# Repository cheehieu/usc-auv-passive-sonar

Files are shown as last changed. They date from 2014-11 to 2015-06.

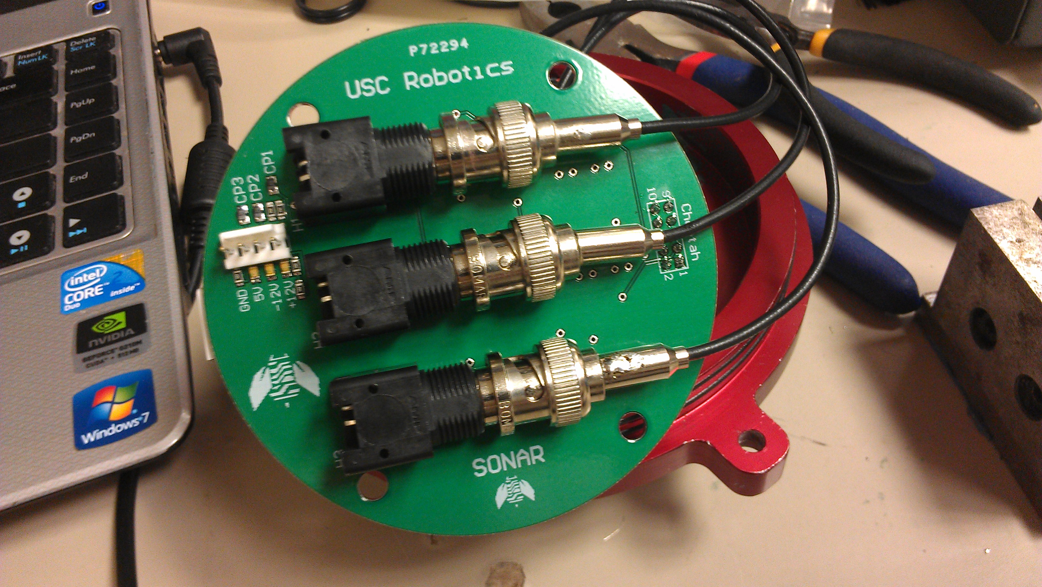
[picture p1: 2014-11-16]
images/IMAG0548.jpg

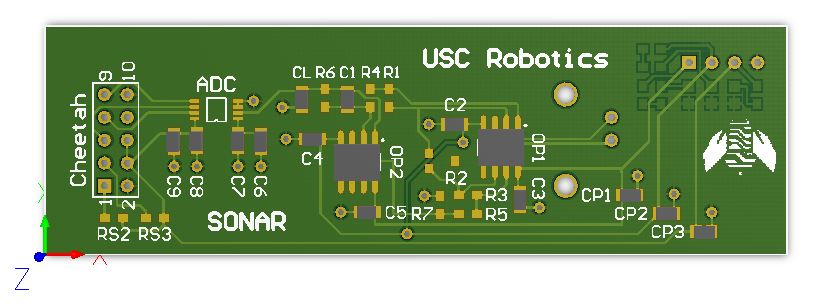
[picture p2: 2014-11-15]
images/sonarDAQ_single.JPG

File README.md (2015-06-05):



## Overview
One of the main tasks of the international AUVSI Robosub competition involves locating the source of an acoustic underwater pinger. This pinger is mounted somewhere on the floor of a 100m wide pool. It emits a 20-30kHz ping every 2 seconds for a duration of 1.3ms. The high level task is to use this ping signal to guide the AUV to a specific location in the pool. 

Our approach was to use an array of three hydrophones oriented in a precise geometric configuration, then use angle-of-arrival calculations to determine the direction of the ping source. To do this, we needed to ensure a clean analog signal from the hydrophones. A custom PCB was designed to perform high speed signal conditioning and data acquisition. This data could then be processed with a series of filters and phase comparisons, which result in ping detection and calculating a desired heading for the AUV.

Because this project spanned the mixed signal domain, a lot of prototyping and testing was done to ensure functionality. Below is an early stage whiteboarding of the signal path, from hydrophone input to robot actuation.



## Hardware
Like most electronic components on the AUV, the hydrophones and sonar board are housed in a double o-ring sealed cylindrical aluminium enclosure. Waterproof Fischer connectors are used to interface the power and data signals of the sonar board with the main CPU. The enclosure and hydrophones are mounted in an equilateral triangle configuration at the bottom of the AUV.

A previous approach to the passive sonar project involved using a triangular array of 3 hydrophones and passive electrical components to isolate and amplify the energy of a wave packet. The signals from the hydrophones were digitized using ADCs, and a Cheetah SPI Host Adapter (an off-the-shelf high-speed communication tool for facilitating the data streaming over an SPI serial bus). The digital information was processed by a microcontroller for its frequency content, and a ping-detection algorithm was used. This involved extracting the phase information and converting the time-difference-of-arrival into an angle towards the pinger. The main issues were signal strength and signal noise, as there appeared to be a lot of interference and cross-talk.



This time around, we are exploring two different approaches. One approach uses a narrow switched capacitor bandpass filter to isolate the 20-30kHz ping signal, an high-gain amplifier to clip the signal (essentially turning it into a square wave), and a phase comparator to determine the phase differences between the different hydrophone channels. The phase comparators will output a pulse width proportional to the phase difference, which is then read by an Arduino microcontroller.

The second approach is an analog frontend improvement of last year’s Cheetah solution. The grounds of each hydrophone channel will be kept separated, and differential-pair hardware will be used to reduce the interference, cross-talk, and external noise. The signals from the hydrophones can be very weak so a low-noise preamplifier will be used to boost and condition the signal for the bandpass filter. Also, faster and more precise ADCs will be used, and a fourth hydrophone will be incorporated into a tetrahedron-like configuration to add another dimension to our calculations.

A circular PCB was designed to fit into the small cylindrical enclosure and interface with all three hydrophones. One prototype is shown below from layout to board bringup.






## Software
Because the AUV ran on a ROS framework, the sonar node was written to post ROS messages to indicate signal strength and direction. The sonar software took many sample conversions from the ADCs through the high-speed SPI buffer on the Cheetah. The data points were analyzed for their frequency content using a digital fast Fourier transform and bandpass filters.

Here, some test data was saved into a CSV text file and plotted in Octave. The "Overlay" plot represents a phase comparison of the input subplot signals.



A windowing time binning algorithm was used to determine if the signal was indeed a ping. Using all data input streams from the three hydrophones, the signal phase can be compared to determine an angle-of-arrival.



## 3D
<iframe width="640" height="480" src="https://sketchfab.com/models/2c645406e3c548b1852d1a6a05af44f1/embed" frameborder="0" allowfullscreen mozallowfullscreen="true" webkitallowfullscreen="true" onmousewheel=""></iframe>

<p style="font-size: 13px; font-weight: normal; margin: 5px; color: #4A4A4A;">
    <a href="https://sketchfab.com/models/2c645406e3c548b1852d1a6a05af44f1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" target="_blank" style="font-weight: bold; color: #1CAAD9;">Passive Sonar PCB</a>
    by <a href="https://sketchfab.com/hieu?utm_source=oembed&utm_medium=embed&utm_campaign=2c645406e3c548b1852d1a6a05af44f1" target="_blank" style="font-weight: bold; color: #1CAAD9;">hieu</a>
    on <a href="https://sketchfab.com?utm_source=oembed&utm_medium=embed&utm_campaign=2c645406e3c548b1852d1a6a05af44f1" target="_blank" style="font-weight: bold; color: #1CAAD9;">Sketchfab</a>
</p>

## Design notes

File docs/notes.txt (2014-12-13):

3ADC ()
- input filtering with NPO and silvermica type dielectric capacitors, metal film resistors (pg. 12)
- input range from VGA (1.25V)
- 10uF ceramic or tantalum in parallel with .1uF ceramic capacitor for Vref->GND

- board layout
- PCB with ground plane
- separate analog and digital signal lines
- 10uF surface mount AVX capacitor for VDD (Murata GRM219R60J106M)
- 0.1uF ceramic capacitor for VREF
- capacitors located as close to pins as possible (keep traces short and wide as possible)

VGA (AD8331)
- Each channel contains an LNA that provides user-adjustable input impedance termination, a differential X-AMP VGA, and a pro-grammable gain postamp with adjustable output voltage limiting
- hydrophones have a 1kohm impedance at desired frequencies
- HILO, GAIN, VCM (adjust to 1.5V for 3V ADC)
- values of RFM and CSH, based on LNA input impedance
- VCM, RCLMP, driving 3V ADC's
- get rid of some jumpers to save space

- board layout
- multilayer board with power and ground planes recommended
- blank areas in the signal layers filled with ground plane
- decoupling SM caps for power supply pins
- decoupling ferrite beads for LNA power pins
- 5V regulator for VGA array
- LON/LOP traces as short as possible for coupling caps
- Riz placed near LON pin
- resistors placed close to VGA output pins, VOL/VOH
- short signal traces

Voltage Reg
- aluminum electrolytic or tantalum capacitors
- effective series resistance greater than 0.1ohm, less than 5ohm

Lowpass filter to remove high frequency noise?
BNC connector footprint (vertical or right angle?)
//Hard-wire jumpers
Figure out VGA and ADC special inputs/outputs
Mounting drill holes
Arduino pin to LED
Trace length for diff pairs (VGA to ADC)
Place ADC on back of board (upside down)
Arduino's max PWM frequency is 62500Hz
Cheetah and Arduino header connectors spacing
Include low pass (band pass filter)
Thicker power and ground traces
Fix Gain2 LPF

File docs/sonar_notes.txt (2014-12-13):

10Mhz Cheetah clock
3kHz sine wave, 1VPP
+/- 2.5V input
clipping?

Reading data from an ADC with the Cheetah:
---SET UP COMMAND QUEUE---
- Call ch_spi_queue_clear to clear the command queue.
- Call ch_spi_queue_oe to add a command to the queue to enable the Cheetah device’s outputs on the SPI bus.
- Call ch_spi_queue_ss to add a command to the queue to enable the slave select signal.
- Call ch_spi_queue_byte and ch_spi_queue_array to queue data to be sent across the SPI bus
- Call ch_spi_queue_ss to queue a command to disable the slave select signal
- Optionally, call ch_spi_queue_oe to queue a command to disable the outputs of the Cheetah device.
- Call ch_spi_batch_shift to send the accumulated accumulated commands across the SPI bus.

Note:
Please note that the queue is not cleared after it has been executed. This allows the same
queue to be executed multiple times without re-queuing commands. The only way to clear a
queue is by calling ch_spi_queue_clear.

If the user wishes to repeat the exact same shift sequence on the bus, the last step can be
executed without the preceding ones. Also, the OE enable commands and SS assert/deassert
commands are held persistent on the Cheetah device. 

---SEND SEVERAL SEPARATE SPI PACKETS---
1. Assert the OE.
2. Assert the appropriate SS, queue the data, and deassert SS.
3. Add optional delay on the bus.
4. Assert the appropriate SS, queue the data, and deassert SS.
5. Repeat the last two steps as many times as desired.
6. Call the batch shift function.

There is an alternative, non-blocking implementation that
can be used in lieu of ch_spi_batch_shift. The functions ch_spi_async_submit and
ch_spi_async_collect allow the user to submit a batch queue and perform other tasks (including
assembling and submitting a subsequent queue) before collecting the results of the initial SPI shift operation. 

---PROCESSING ASYNC DATA---
1. Submit 2–4 asynchronous batches, each with about 40 ms worth of SPI shifting. A single batch can contain many SPI commands / packets, of course.
2. Call ch_spi_async_collect to collect one batch. Signal another thread to process this data.
3. Submit another asynchronous batch to replace the one that was just collected.
4. Repeat steps 2 & 3 while your other thread simply processes the data.

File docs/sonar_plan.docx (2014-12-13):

SONAR PROJECT

Test Bed Design

- Oscillator board
- Phase difference board
  - phase shift board to simulate pinger location
  - function generator tests

Analog Board

- ~~Hydrophone maintenance~~
  - ~~(3x) RESON TC4013 Hydrophones~~
  - ~~Spaced 24mm apart in triangle at bottom of sub~~
- ~~Pinger~~
  - ~~Output:~~ ~~22, 23, 24, 25, 26, 27, 28, 29 or 30 kHz~~
  - ~~Pings at 0.5 Hz (2 seconds) for 1.3ms with a sound level of 187 dB~~
  - ~~Separated by 0.9 seconds from practice pool ping~~
- Filter Design
  - Switched Capacitor Filter
    - Narrow bandpass for 20Khz to 40Khz range
    - Controlled by clock frequency in the 0-40Mhz range
    - MAX263
      - Supply voltage: 15V
      - Clock input (2.4min High, 0.8max Low)
  - Infinite Gain Amplifier
    - opamp
  - Phase Difference

Digital Board

- Microcontroller Board (interface with phase diff)
- Programmable Oscillator
  - Maxim DS1077, DS1085
  - Frequency range of 66-133MHz, adjustable over the I2C connection in 10KHz intervals
  - This is fed into a programmable divisor of 1-1025, making for a wide range of available output values
  - Pinout, voltage/current requirements
- Carrier Board >> Arduino >> Progammable Oscillator >> Switched Capacitor Filter
- Microcontroller software (Arduino)

ROS Sonar Node

- Messages (Dave’s implementation)
  - Pinger ID (#0 correct, #1 incorrect)
  - Heading
  - Magnitude
  - TimeSince
- PingerArray

Pinger >> water >> hydrophones >> VGA >> filter >> ADC >> Cheetah SPI >> ROS Sonar Node

Pinger >> water >> hydrophones >> preamp >> filter >> opamp >> ADC >> Cheetah SPI >> Sonar Node

Pinger >> water >> hydrophones >> preamp >> filter >> >> opamp >> phase comparator >> ADC >> Sonar Node

~~Pinger operation (~~~~turn on,~~ ~~set frequency, mount underwater~~~~, two~~ ~~pingers~~~~, interference~~~~)~~

~~Signal capture through hydrophones/connecters~~ ~~(compare/test signal amplitudes, signal degradation?)~~

~~Pre-amp to boost signal for filter?~~ ~~VGA~~~~. Signal conditioning~~

Signal filtering (test for filtered output, add noise)

- Switched cap filter input (function generator sine wave at 25kHz, 100mV)
- Clock input (function generator, square wave at 1MHz, 5V, interface with oscillator after)
- Variable frequency oscillator
- Supply voltage, control words (pin programmable with Arduino), operating modes, Qs, fclk/f0 ratio, cascading?
- MAX7490

Amplification

- Input (func gen to simulate filtered signal)
- Op-amp (gain to clip signal and turn into square wave), differential amplifier for low noise
- Zero crossing detector, rectifier, multilateration

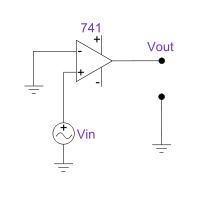
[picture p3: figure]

- San Diego City used 100X gain

Filtered signal acquisition (ADCs, Cheetah sampling)

- Hook up ADC to func gen (DC voltage, sinusoid, square wave)
- Arduino to take in bytes from ADC (plot and verify)
- Repeat with Cheetah at faster sampling rates
- AD7865 simultaneous sampling four channel 14-bit ADC
- Clipped input from amplifier does not exceed voltage requirements? Clamping? Op-amp supply voltage
- FFT to find phase difference

Phase comparator

- Outputs a PWM signal whose pulse width is proportional to the difference in phase between the two signals
- MAX9382
- PWM signal goes to microcontroller to determine how long the pulse width is
- Pulse width is converted to a left or right degree error (directional error) by a look up table
- San Diego city uses 4 hydrophones mounted at 45 degrees to vertical, to determine when sub is right above the pinger
- PLL phase locked loop
  - A type II detector is sensitive only to the relative timing of the edges of the input and reference pulses, and produces a constant output proportional to phase difference when both signals are at the same frequency.

Ping detection (measure length of time, bin, windows)

- Analog voltage threshold triggers sampling and storing in serial memory
- Cross-correlation algorithm is performed on binned signal return samples to find phase differences
- Wait for min amplitude, accumulate samples, apply band pass filter on samples, calculate phase difference between hydrophones (reference channel and remaining), send phase difference, compare in lookup table for heading and elevation (value in the table with smallest difference)

Phase difference analyzer (angle-of-arrival calculation, closest hydrophone pair, 3rd hydrophone)

- From each hydrophone pair, two candidate rotation angles are found. The two angles which are closest to each other gives the final estimate of rotation needed to aim toward the pinger

Localization (sensor data for direction, phase difference tells you distance from source)

Test on SeaBee

Run 3-channels, triangulation

Analog filtering, digital signal processing

Cornell can compute heading and elevation to the pinger within one degree (4 hydrophones)

Hyperbolic positioning to determine directional vector towards the pinger

Distance between hydrophones is less than half the wavelength, to ensure unambiguous phase difference → along with physical placement of h-phones and speed of sound underwater, can determine the time difference and calculate angle of sound source

FPGA? DSP?

repurpose VGA for pressure sensor?

Parts lists and cost breakdown

Break up into smaller tasks (amplifier, phase comparator, ADC, find pinger)

Jose
Current Milestone: Finish bandpass filter
Date: October 11th

Dylan
Current Milestone: Test bed oscillator
Date: September 20th

I'll start with the system as it was for the competition last year:

Hardware:

- (3x) RESON TC4013 Hydrophones (http://www.reson.com/wp-content/uploads/2010/12/TC4013.pdf)
- Cheetah SPI Host Adapter (http://www.totalphase.com/products/cheetah_spi/)
- LTC1400 12-Bit, 400ksps ADC (http://cds.linear.com/docs/Datasheet/1400fa.pdf)
- Custom PCB (Beosub Repository)
  - trunk/Electrical/Eagle/Wave Packet Sonar/SonarCheetah.brd
  - trunk/Electrical/Eagle/Wave Packet Sonar/SonarCheetah.sch

Signal Path:

Pinger >> ~~~ water ~~~ >> hydrophones >> ADC >> Cheetah SPI >> ROS Sonar Node

Software:

- Initial Dev
  - Saliency Repository
    - src/Robots/SeaBeeIII/Sonar
- Current
  - ROS Node (http://code.google.com/p/seabee3-ros-pkg/)
- FFTW3 - FFT Library (http://www.fftw.org/)

Walkthrough:

- The initial dev software folder contains all of the testing software and development/experimentation code I initially used to determine how to approach coding the phase difference algorithm, frequency testing, Cheetah communications, etc...
- The ROS node is the most current version of the code (originally written for Box Turtle, but should be ok with C Turtle as well)
- Cheetah SPI (as configured in ROS node code)
  - NOTE: At the time only the 32-bit pre-compiled shared library was provided, so be aware of this when running / compiling on 64-bit systems
  - Communicates in asynchronous mode to keep actual sampling rates up
  - "True" sampling rate is calculated based on the speed of the Cheetah at runtime using a linear interpolation method from experimental data (signal generator, spectrogram, and max frequency bin identifier)
    - Initially I tried calculating this real-time in the principle loop but had major inaccuracies
    - Talked with Rand & Edward about it, but didn't come up with a function fix / solution, so went with the existing approximation
  - Uses slave select (SS) signals as convert (CONV) signals for ADCs
  - Generates a batch of conversions, which will occur in rapid succession without interruption once submitted
  - The collected data stream comes back as individual bytes, but the ADC output data is a combination of two consecutive bytes and must be combined so relevant information can be extracted (data, ready bit, etc.) See ADC data sheet for spec and code for implementation
  - The extracted (valid) data is stored in their respective signal buffers corresponding to the 3 hydrophones
- Ping Detection
  - Each buffer is examined with a short sliding window for significant frequency content in the expected FFT bin
    - Since the window is short, the frequency resolution is poor but the temporal resolution is high so a full ping can be isolated in time with reasonable granularity
  - A running sample mean is kept to evaluate whether or not the current value of the FFT bin is large enough to be considered a peak
  - If peaks are found in all channels, an indicator is noted for that time step
    - This continues until the current time step does not have an indicator
  - Once a peak is not detected, the run of indicators is checked for sufficient length (i.e. was it a full ping, or just a small error)
  - The history data corresponding to all blocks marked with a positive indicator are extracted an an FFT is performed on the full ping sequence
    - The increased length of the FFT will provide more accurate frequency resolution and allow the phase information from just the ping frequency to be extracted
- Angle Calculation
  - An optimal-pair phase difference angle-of-arrival (http://en.wikipedia.org/wiki/Angle_of_arrival) algorithm was developed by Rand and I for relative angle estimation of sonar pingers
  - The best hydrophone pair is determined by finding the minimum phase difference between hydrophone pairs
  - The phase difference is adjusted for a phase factor (rear vs. front) using the remaining hydrophone
  - The phase difference is adjusted for an angular offset base on the chosen hydrophone pair
  - Angle estimate is calculated using the physical separation of the hydrophones

Problems:

- Signal strength
  - When the cables were redone just before the competition, the signal strength dropped significantly to the point that the peak detection stopped working
  - The cable attachements need to be redone and the analog front end (following section) will help with this
- Signal quality (SNR)
  - Without hardware filtering, the only signal isolation occurs through the FFT
  - Ambient noise and common hydrophone grounds cause significant phase distortions that decrease the accuracy of the angle estimate

Now the more recent work & future directions:

Proposed New Hardware (Experimental):

- LTC1569CS8-7 - Linear Phase, DC Accurate, Tunable 10th Order Lowpass Filter (http://cds.linear.com/docs/Datasheet/15697fs.pdf)
- AD8331ARQZ-ND - Single Variable-Gain Amplifier (VGA) with Ultralow Noise Preamplifier and Programmable RIN (http://www.analog.com/static/imported-files/Data_Sheets/AD8331_8332_8334.pdf)
- LTC1403ACMSE-1 - Serial 14-Bit, 2.8Msps ADC (http://www.linear.com/pc/downloadDocument.do?navId=H0,C1,C1155,C1001,C1158,P2481,D1475)
- Simple Arduino / Amtel chip to sample the signal path & control the VGA

This set of hardware was my initial suggestion for a revised analog frontend that filters out high-frequency noise (tunable filter), keeps the signal amplitude high (VGA), and samples with more precision at higher frequency (new ADC). I'm happy with the idea, but I think to really address the problems we had with the sampling we need to use differential pair hardware and separate the grounds of the signal channels, which should remove a significant amount of interference; Since the signal paths would be independent differential pairs, the cross-talk & external noise will essentially be removed. More research needs to be done to figure out what hardware should be used.

Signal Path:

Pinger >> ~~~ water ~~~ >> hydrophones >> VGA >> filter >> ADC >> Cheetah SPI >> ROS Sonar Node

DIAGNOSTIC BOARD

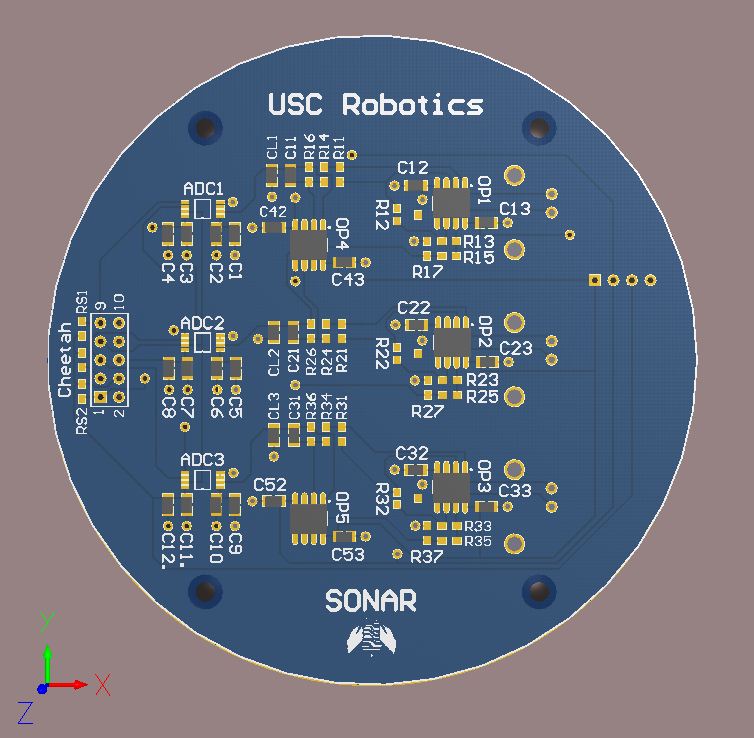
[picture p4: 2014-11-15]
images/sonarDAQ.JPG

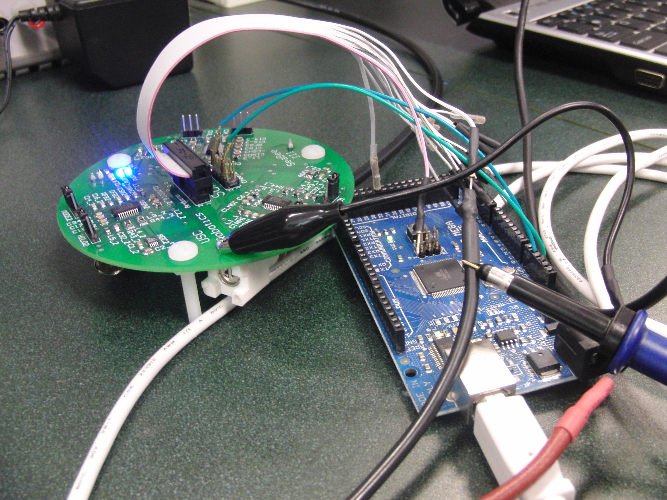
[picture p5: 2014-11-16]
images/CIMG1183.JPG

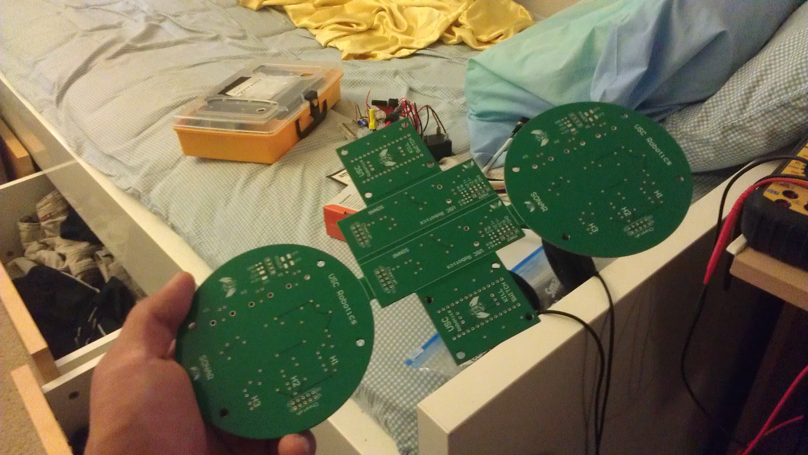
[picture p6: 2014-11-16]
images/IMAG0600.jpg

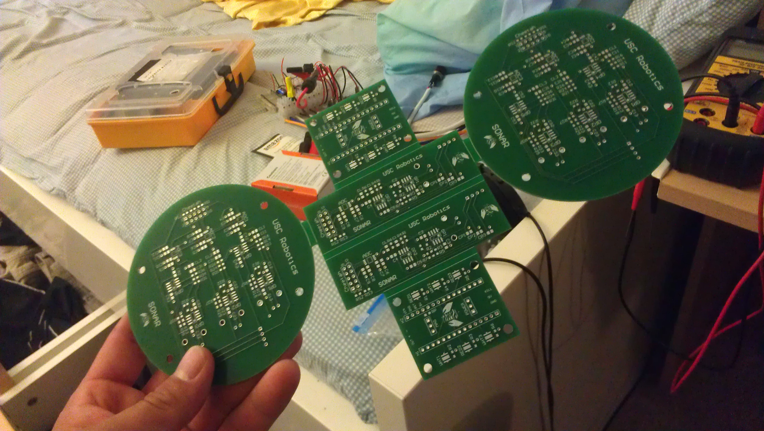
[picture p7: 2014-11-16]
images/IMAG0599.jpg

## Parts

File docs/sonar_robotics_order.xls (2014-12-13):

USC Aerial Robotics
Order Date: 2/1/2012
Part # | Item | Qty | Unit Cost | Total Cost | Link/Order Instruction | Purpose | Payment
Digikey.com
A32261-ND | BNC Female Connector | 5 | $3.48 | $17.40 | http://search.digikey.com/us/en/products/5227161-9/A32261-ND/811159 | Sonar | AMEX
493-4091-1-ND | 2.2uF Tantalum Cap | 10 | $0.46 | $4.60 | http://www.digikey.com/product-detail/en/F920J225MPA/493-4091-1-ND/2529818 | Sonar | AMEX
160-1416-1-ND | 0805 LED | 10 | $0.38 | $3.80 | http://www.digikey.com/product-detail/en/LTST-C170KSKT/160-1416-1-ND/386780 | Sonar | AMEX
490-4612-1-ND | Trimmer Pot | 10 | $0.44 | $4.40 | http://www.digikey.com/product-detail/en/PVZ3G104C01R00/490-4612-1-ND/1203955 | Sonar | AMEX
490-1673-1-ND | 0.1uF Ceramic Cap | 14 | $0.06 | $0.78 | http://search.digikey.com/us/en/products/GRM21BR71E104KA01L/490-1673-1-ND/587412 | Sonar | AMEX
493-2939-1-ND | 4.7uF Electrolytic Cap | 14 | $0.96 | $13.44 | http://www.digikey.com/product-detail/en/F951C475MPAAQ2/493-2939-1-ND/1129228 | Sonar | AMEX | case code P
490-1593-1-ND | 47pF Cap | 10 | $0.37 | $3.72 | http://www.digikey.com/product-detail/en/GRM2195C2A470JZ01D/490-1593-1-ND/587798 | Sonar | AMEX | grm219
490-1664-1-ND | 0.01uF Cap | 10 | $0.04 | $0.39 | http://www.digikey.com/product-detail/en/GRM216R71H103KA01D/490-1664-1-ND/587472 | Sonar | AMEX | grm216, pg8
P10KACT-ND | 10K Resistor | 20 | $0.10 | $2.00 | http://www.digikey.com/product-detail/en/ERJ-6GEYJ103V/P10KACT-ND/43118 | Sonar | AMEX
P1.0KACT-ND | 1K Resistor | 50 | $0.10 | $5.00 | http://www.digikey.com/product-detail/en/ERJ-6GEYJ102V/P1.0KACT-ND/42833 | Sonar | AMEX
LT1113CS8#PBF-ND | SM Opamp | 13 | $6.53 | $84.89 | http://search.digikey.com/us/en/products/LT1113CS8%23PBF/LT1113CS8%23PBF-ND/894415 | Sonar | AMEX
 |  | Order Total: |  | $140.42 | Plus Shipping

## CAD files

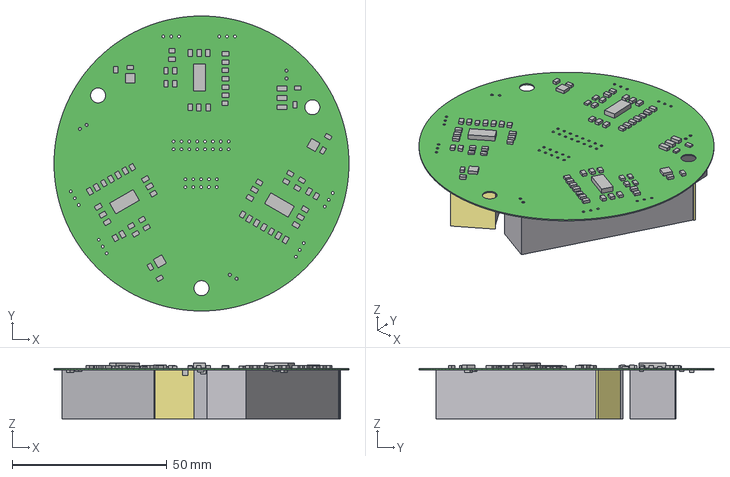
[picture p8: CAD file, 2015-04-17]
hw/Sonar/PCB/sonar.step
95.3 x 95.3 x 18.0 mm
Board
Extruded x 91

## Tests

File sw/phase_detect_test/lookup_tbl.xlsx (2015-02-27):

Phase Difference | PC1 (exp) | PC1 (act) | PC3 (exp) | PC3 (act)
0 | 0.000 | 0.000 | 0.000 | 0.000
10 | 0.278 |  | 0.139
20 | 0.556 | 0.591 | 0.278 | 0.264
30 | 0.833 | 0.767 | 0.417 | 0.367
40 | 1.111 | 0.929 | 0.556 | 0.425
50 | 1.389 | 1.065 | 0.694 | 0.523
60 | 1.667 | 1.266 | 0.833 | 0.616
70 | 1.944 | 1.393 | 0.972 | 0.709
80 | 2.222 | 1.564 | 1.111 | 0.792
90 | 2.500 | 1.730 | 1.250 | 0.865
100 | 2.778 | 1.906 | 1.389 | 0.943
110 | 3.056 | 2.087 | 1.528 | 1.036
120 | 3.333 | 2.219 | 1.667 | 1.119 | 1.603
130 | 3.611 | 2.385 | 1.806 | 1.183 | 1.784
140 | 3.889 | 2.581 | 1.944 | 1.261 | 1.945
150 | 4.167 | 3.994 | 2.083 | 1.354 | 2.063
160 | 4.444 | 3.930 | 2.222 | 1.437 | 2.214
170 | 4.722 | 3.915 | 2.361 | 1.515 | 2.361
180 | 5.000 |  | 2.500
190 |  |  | 2.639
200 |  |  | 2.778
210 |  |  | 2.917
220 |  |  | 3.056
230 |  |  | 3.194
240 |  |  | 3.333
250 |  |  | 3.472
260 |  |  | 3.611
270 |  |  | 3.750
280 |  |  | 3.889
290 |  |  | 4.028
300 |  |  | 4.167
310 |  |  | 4.306
320 |  |  | 4.444
330 |  |  | 4.583
340 |  |  | 4.722
350 |  |  | 4.861
360 |  |  | 5.000

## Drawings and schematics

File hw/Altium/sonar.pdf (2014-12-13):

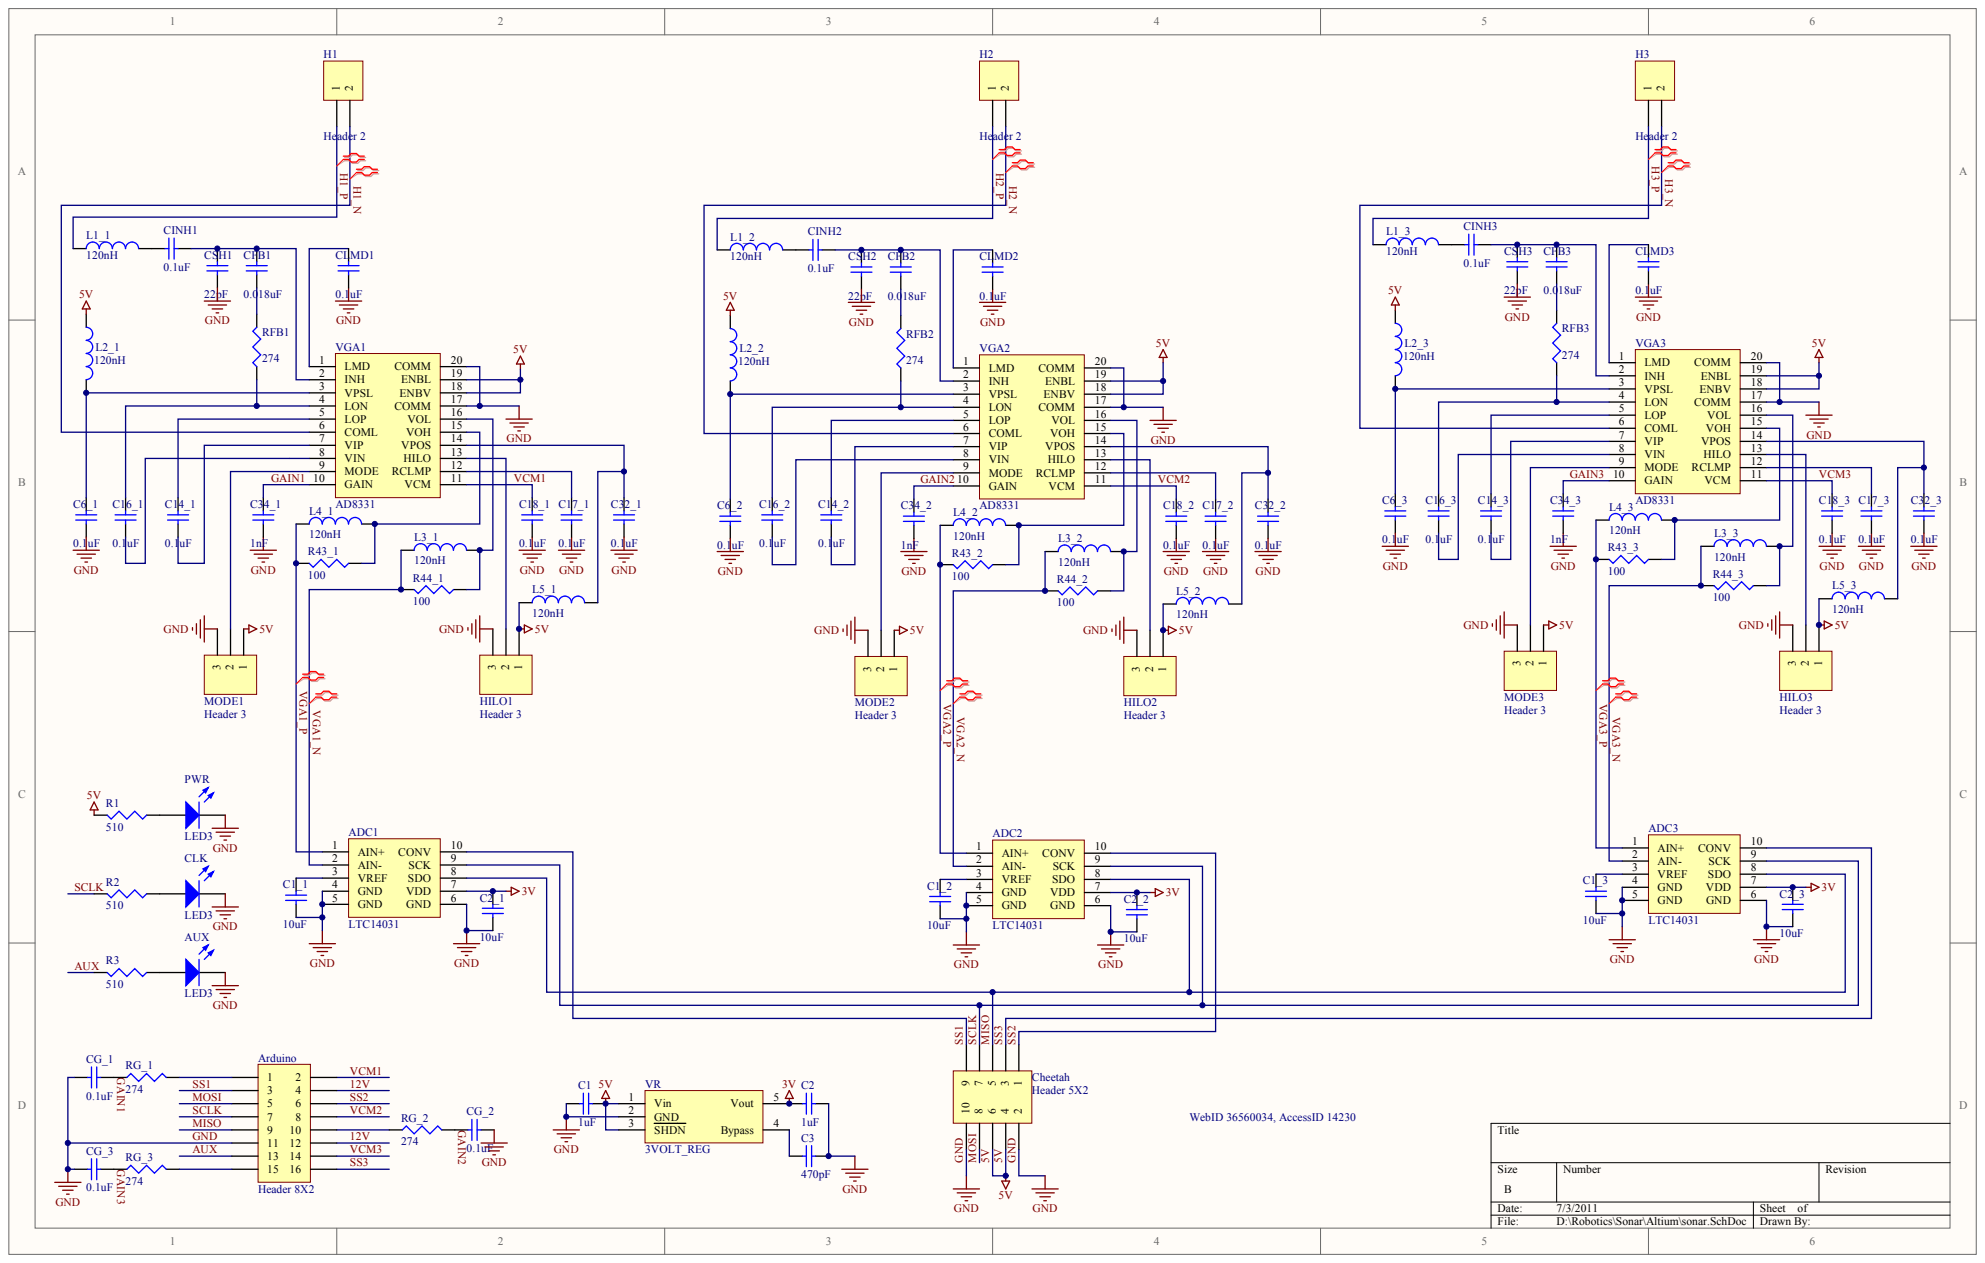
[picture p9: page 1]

VREF 3 | GND 5 VREF 3 | GND | 6 VDD 7 SDO 8 SCK 9 CONV 10 | VREF 3

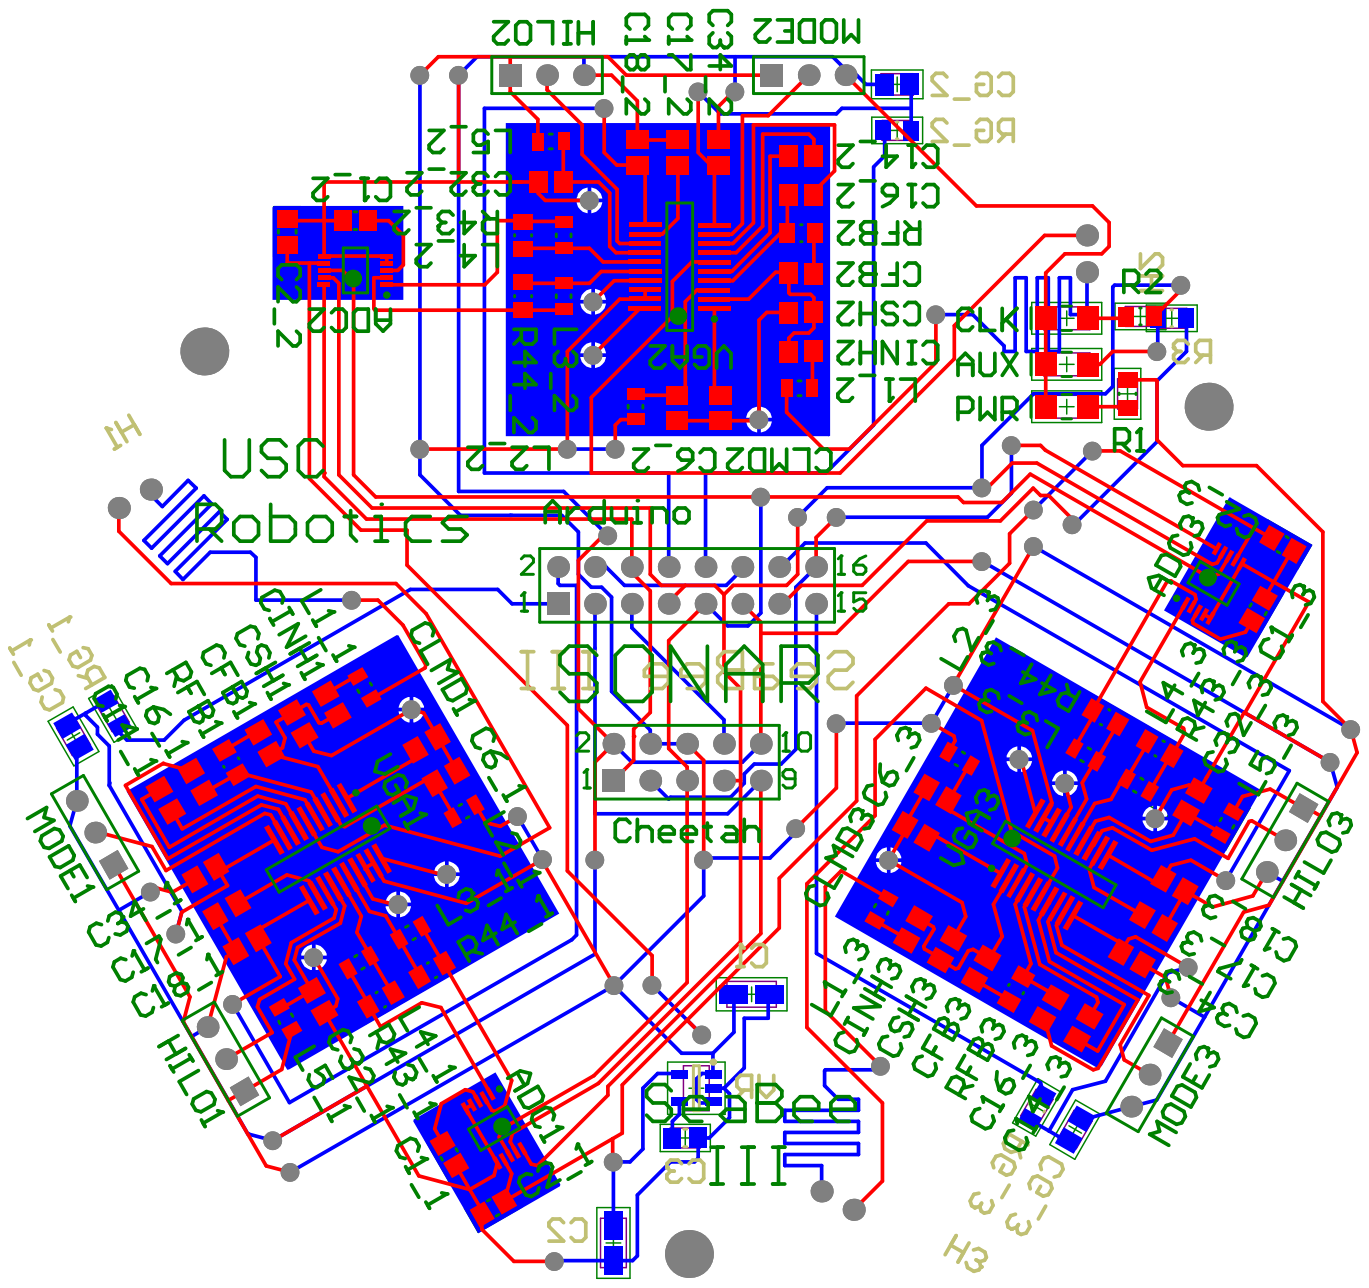
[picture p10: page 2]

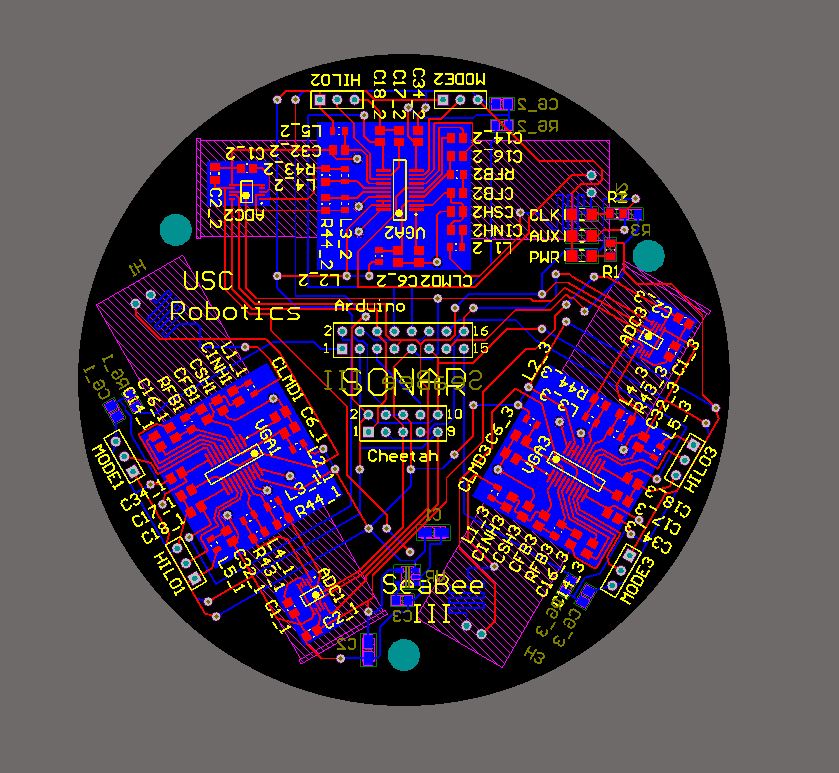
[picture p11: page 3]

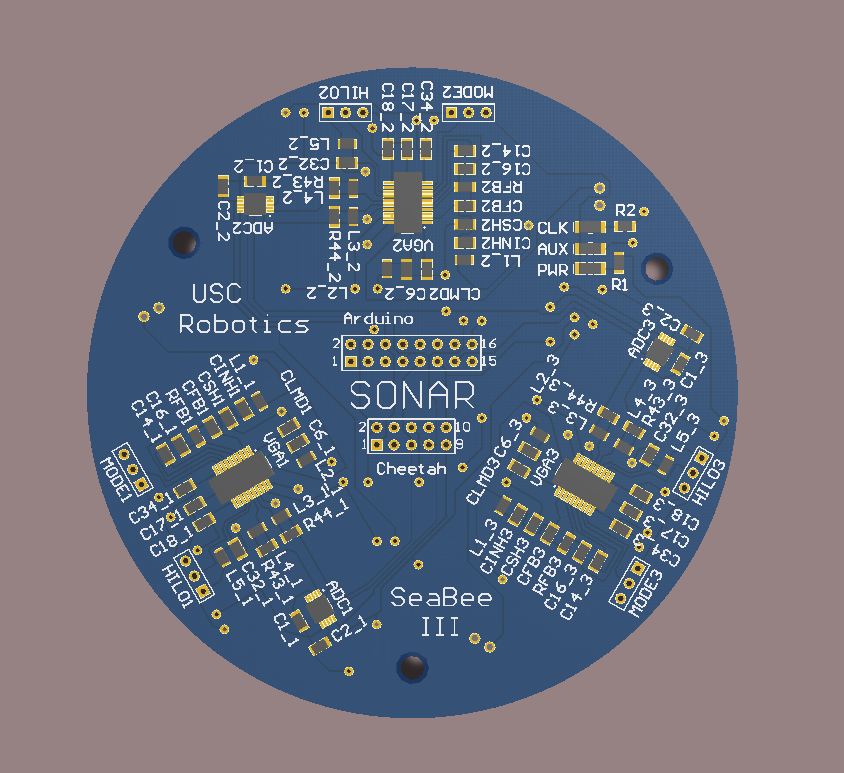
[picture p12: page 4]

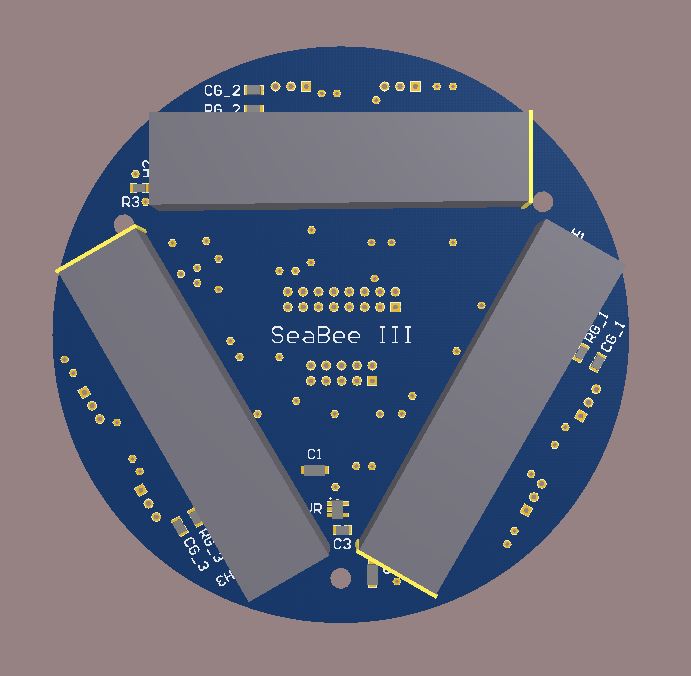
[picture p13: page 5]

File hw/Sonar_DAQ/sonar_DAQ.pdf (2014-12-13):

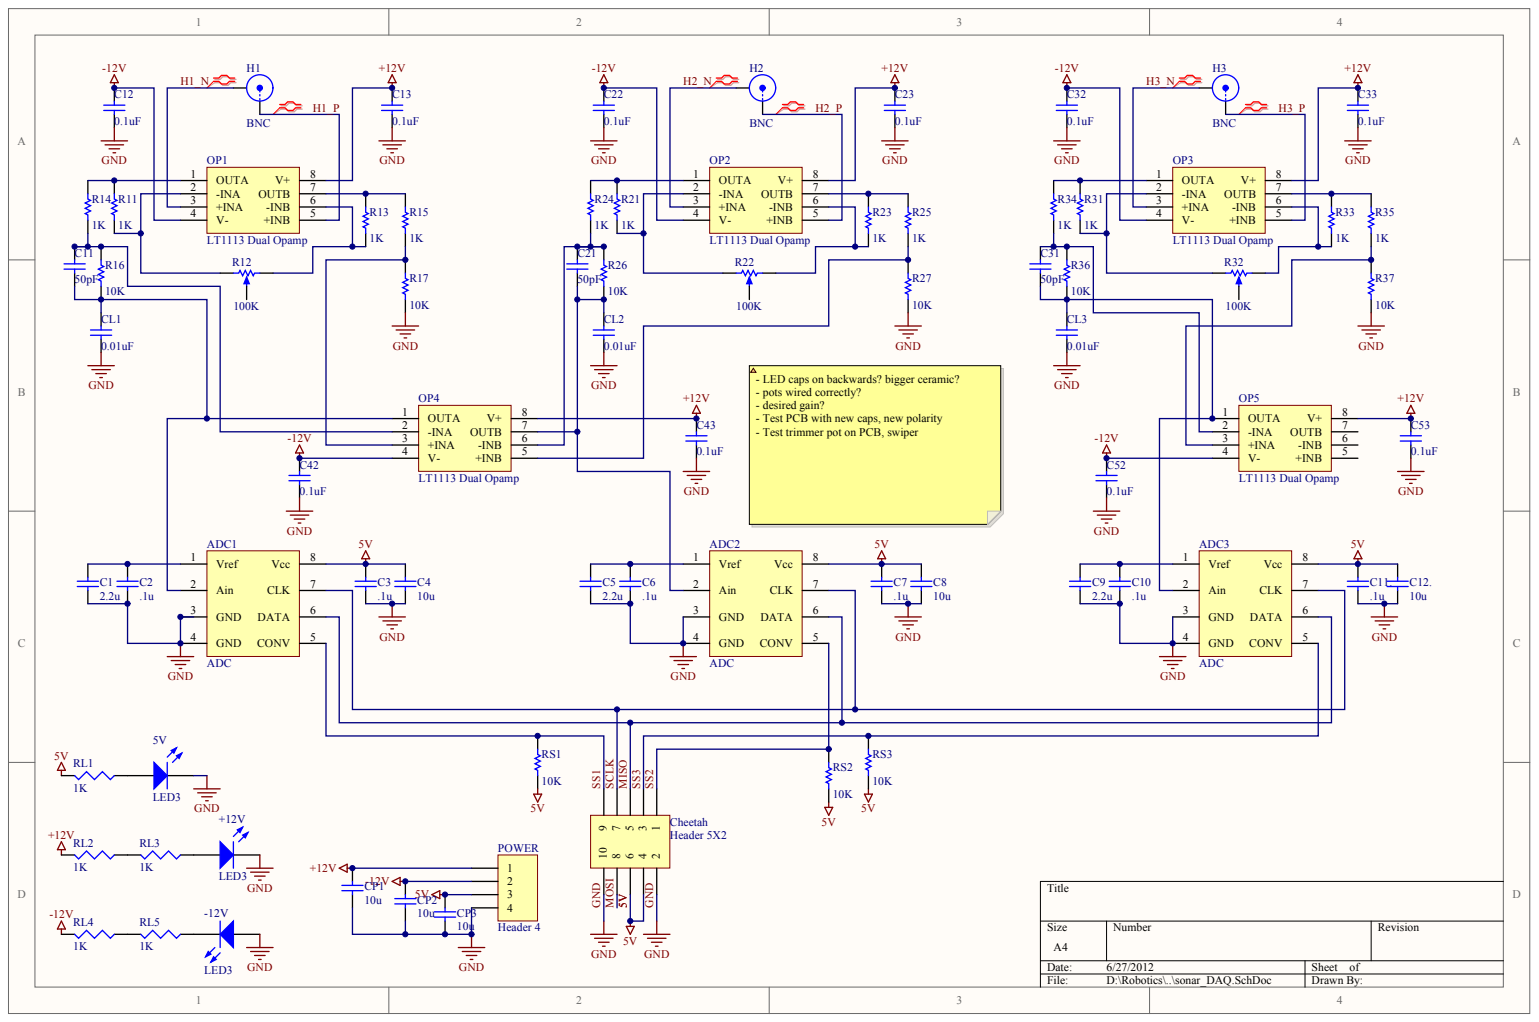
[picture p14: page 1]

- LED caps on backwards? bigger ceramic?
- pots wired correctly?
- desired gain?
- Test PCB with new caps, new polarity
- Test trimmer pot on PCB, swiper

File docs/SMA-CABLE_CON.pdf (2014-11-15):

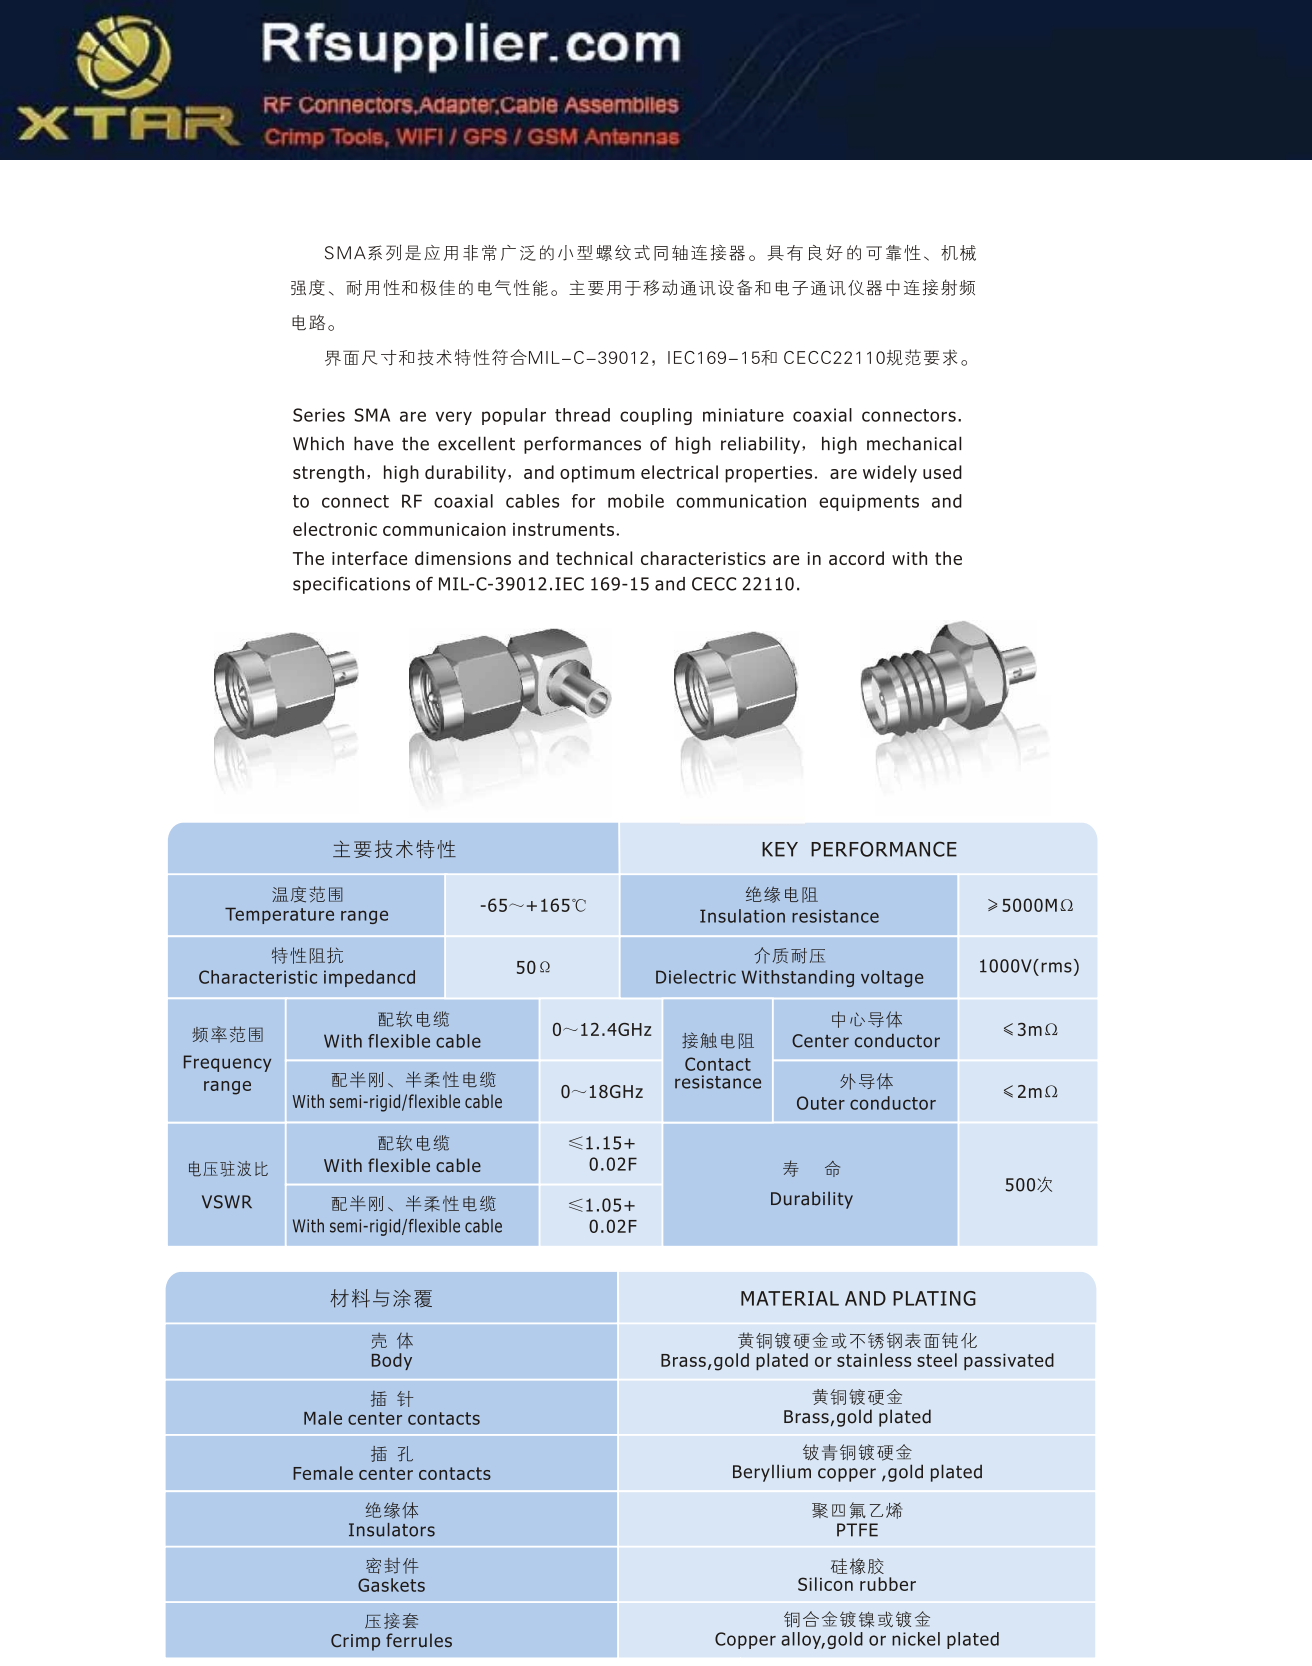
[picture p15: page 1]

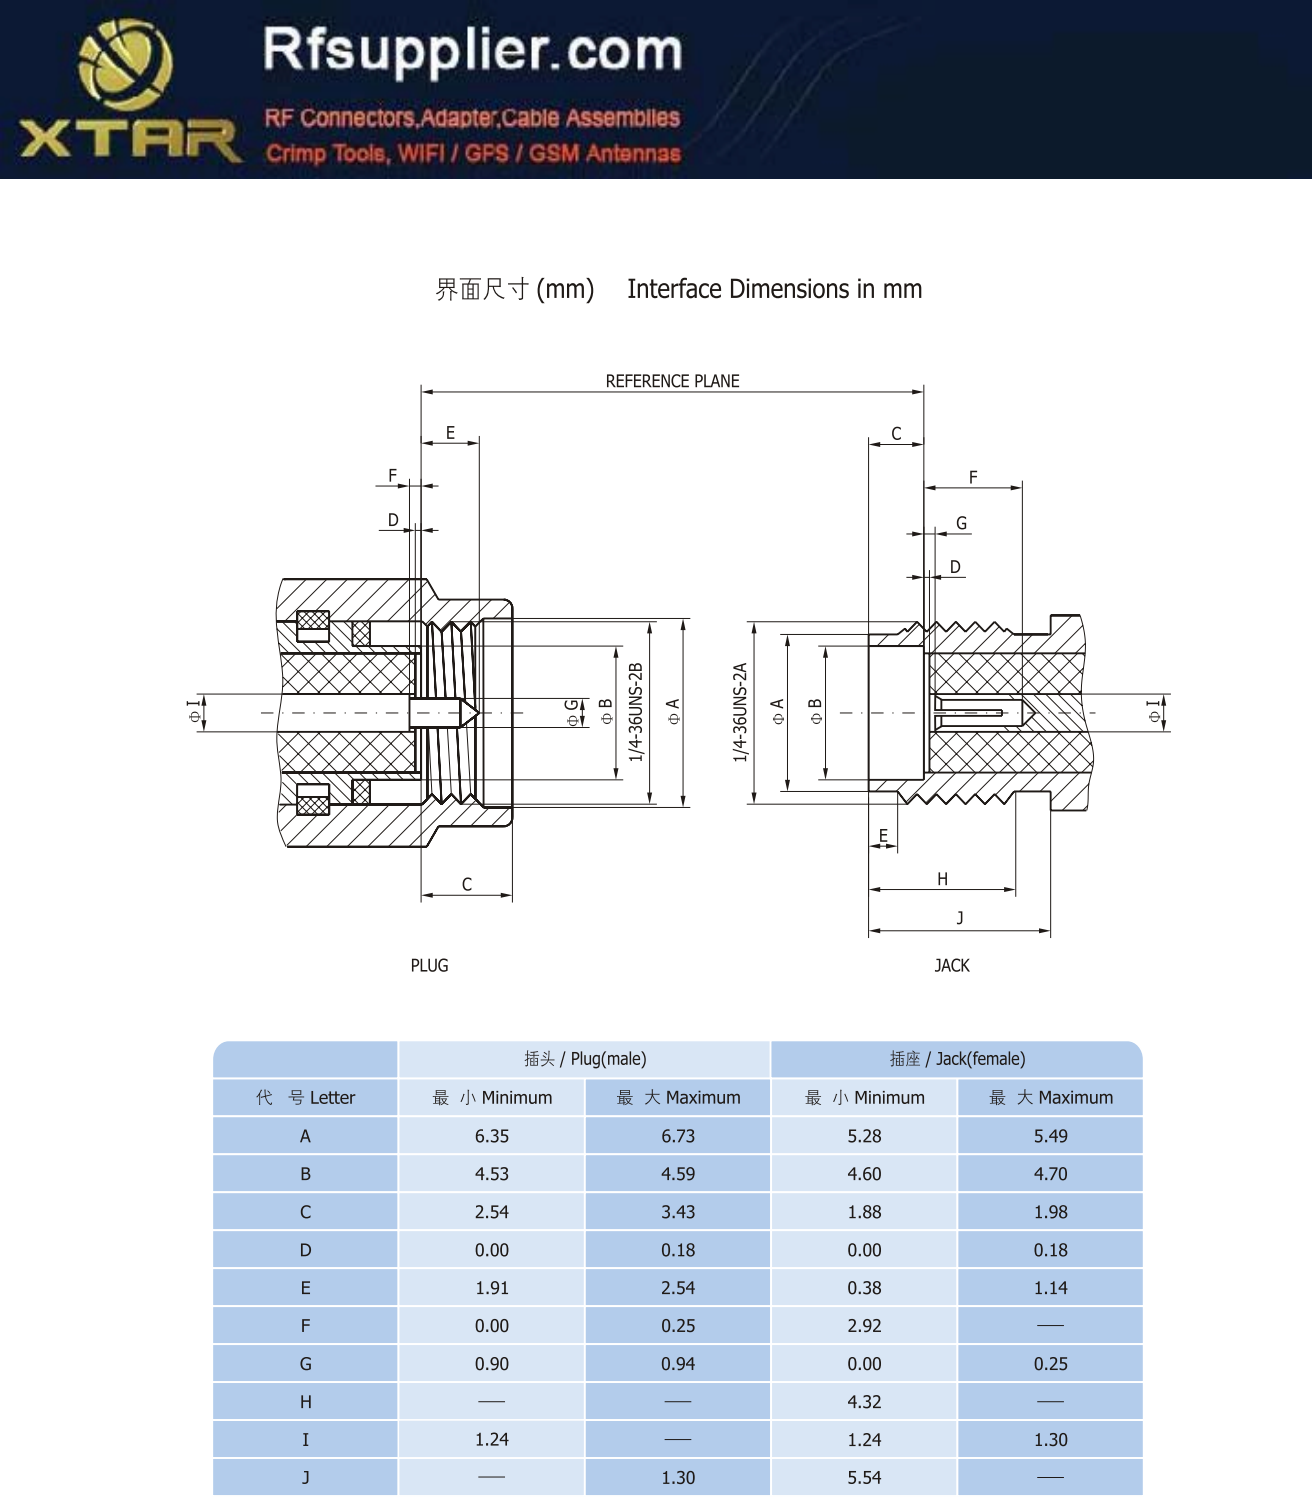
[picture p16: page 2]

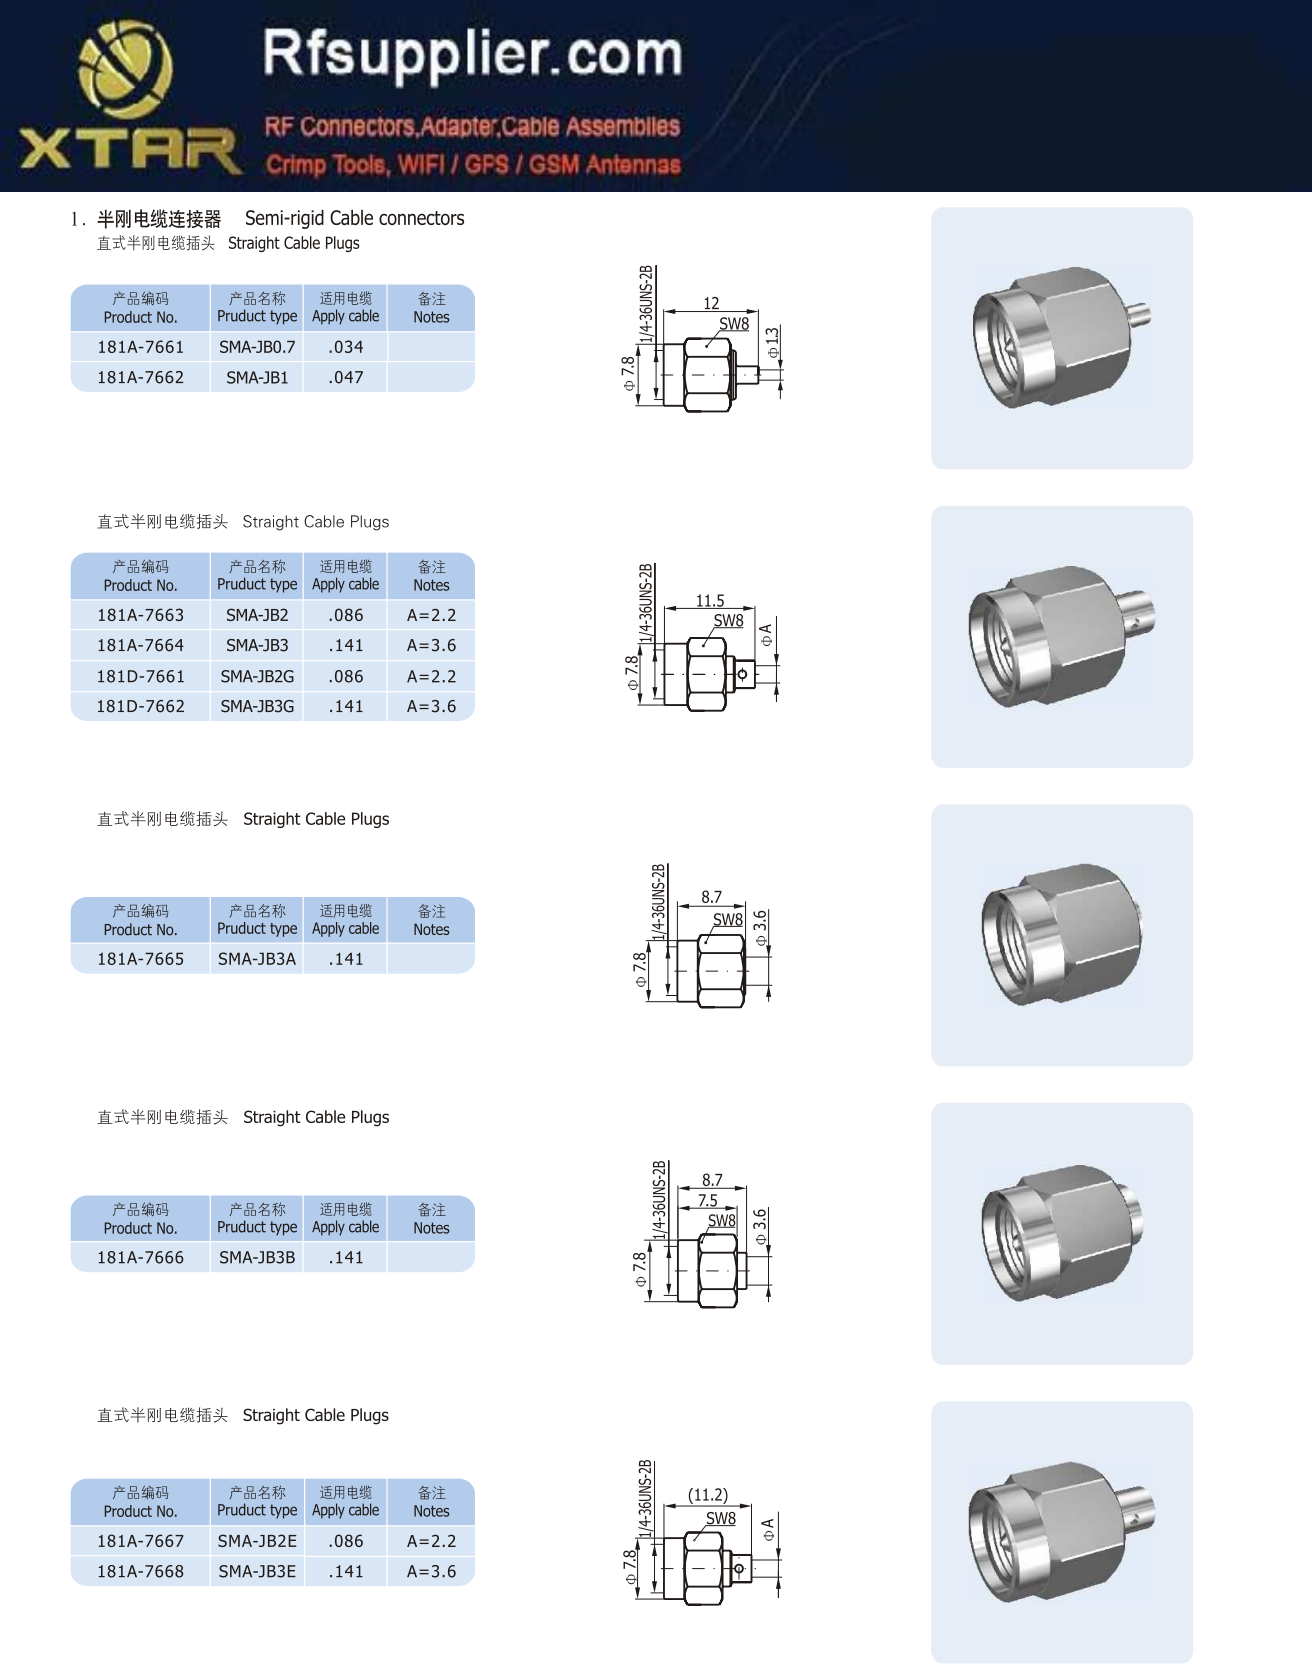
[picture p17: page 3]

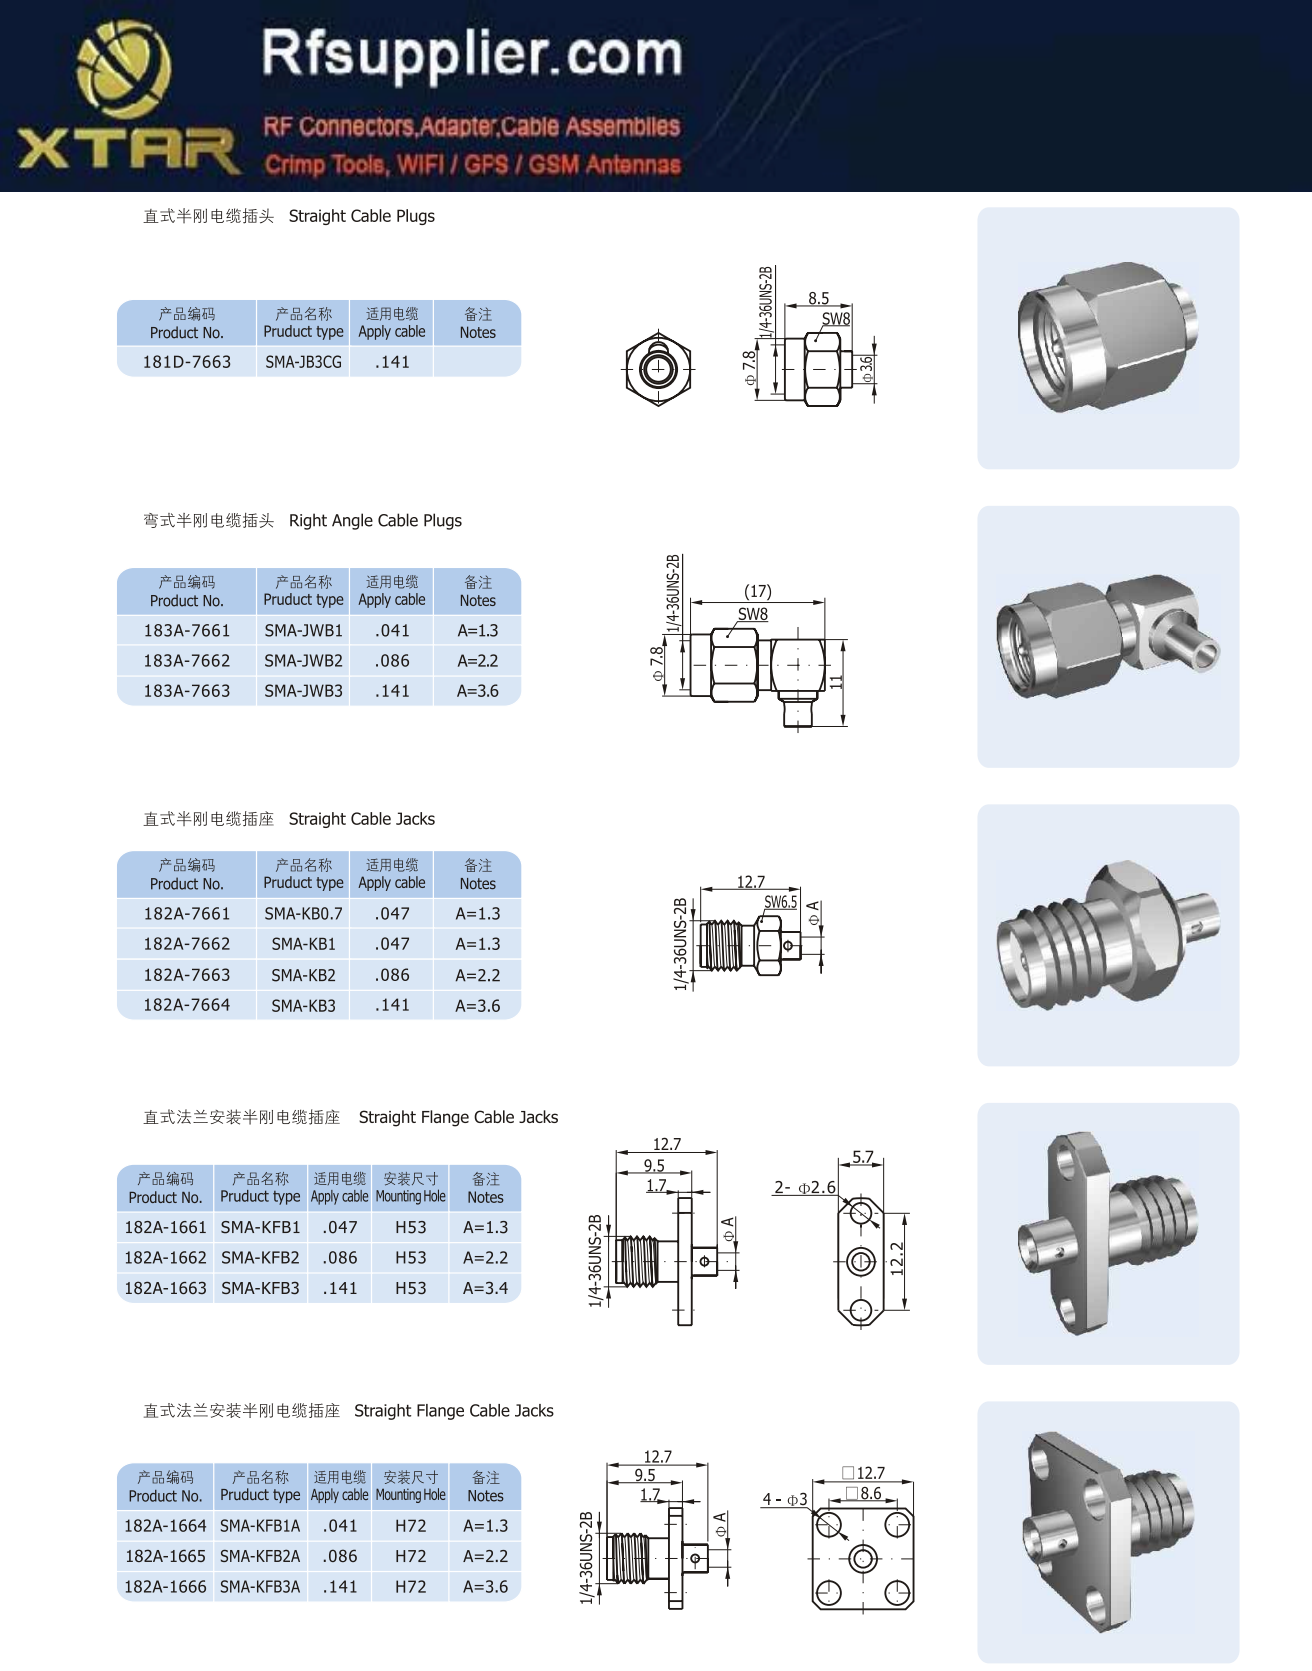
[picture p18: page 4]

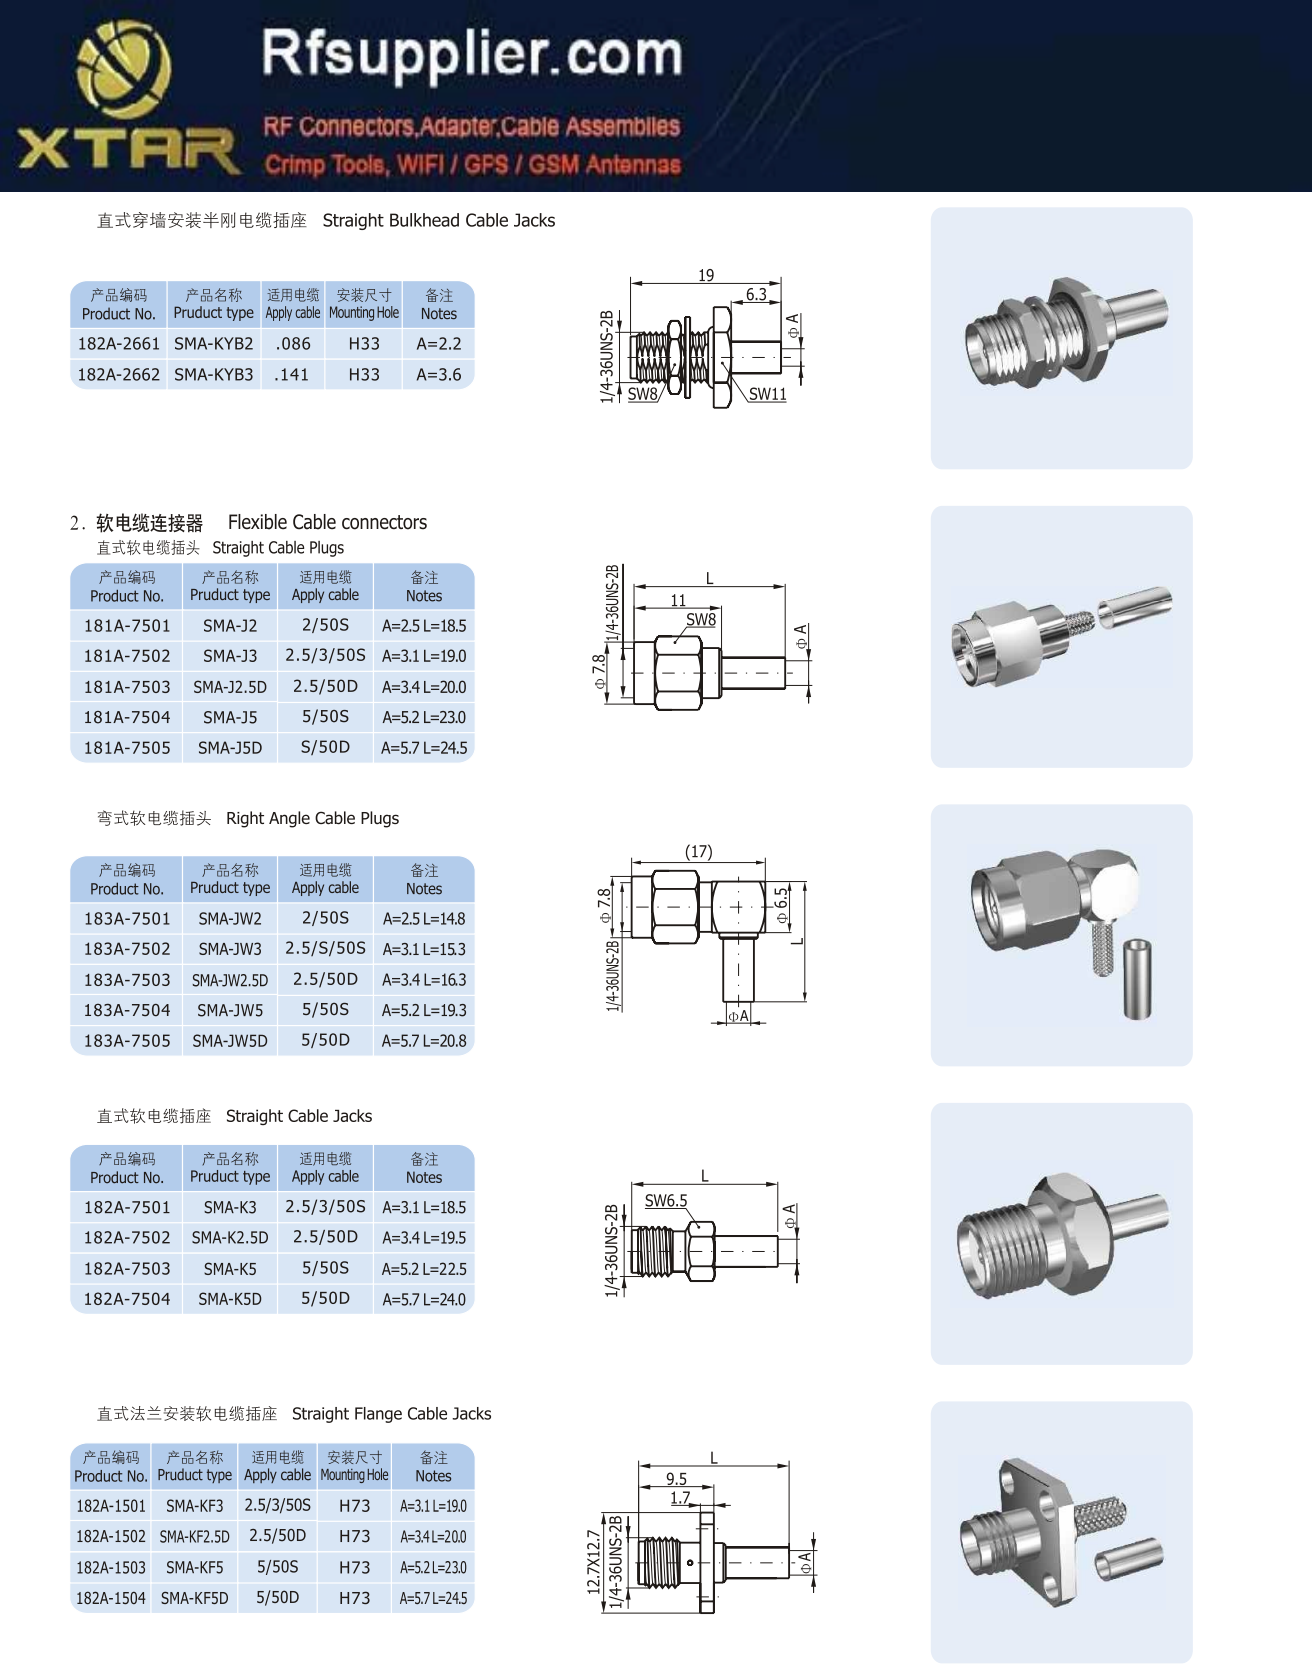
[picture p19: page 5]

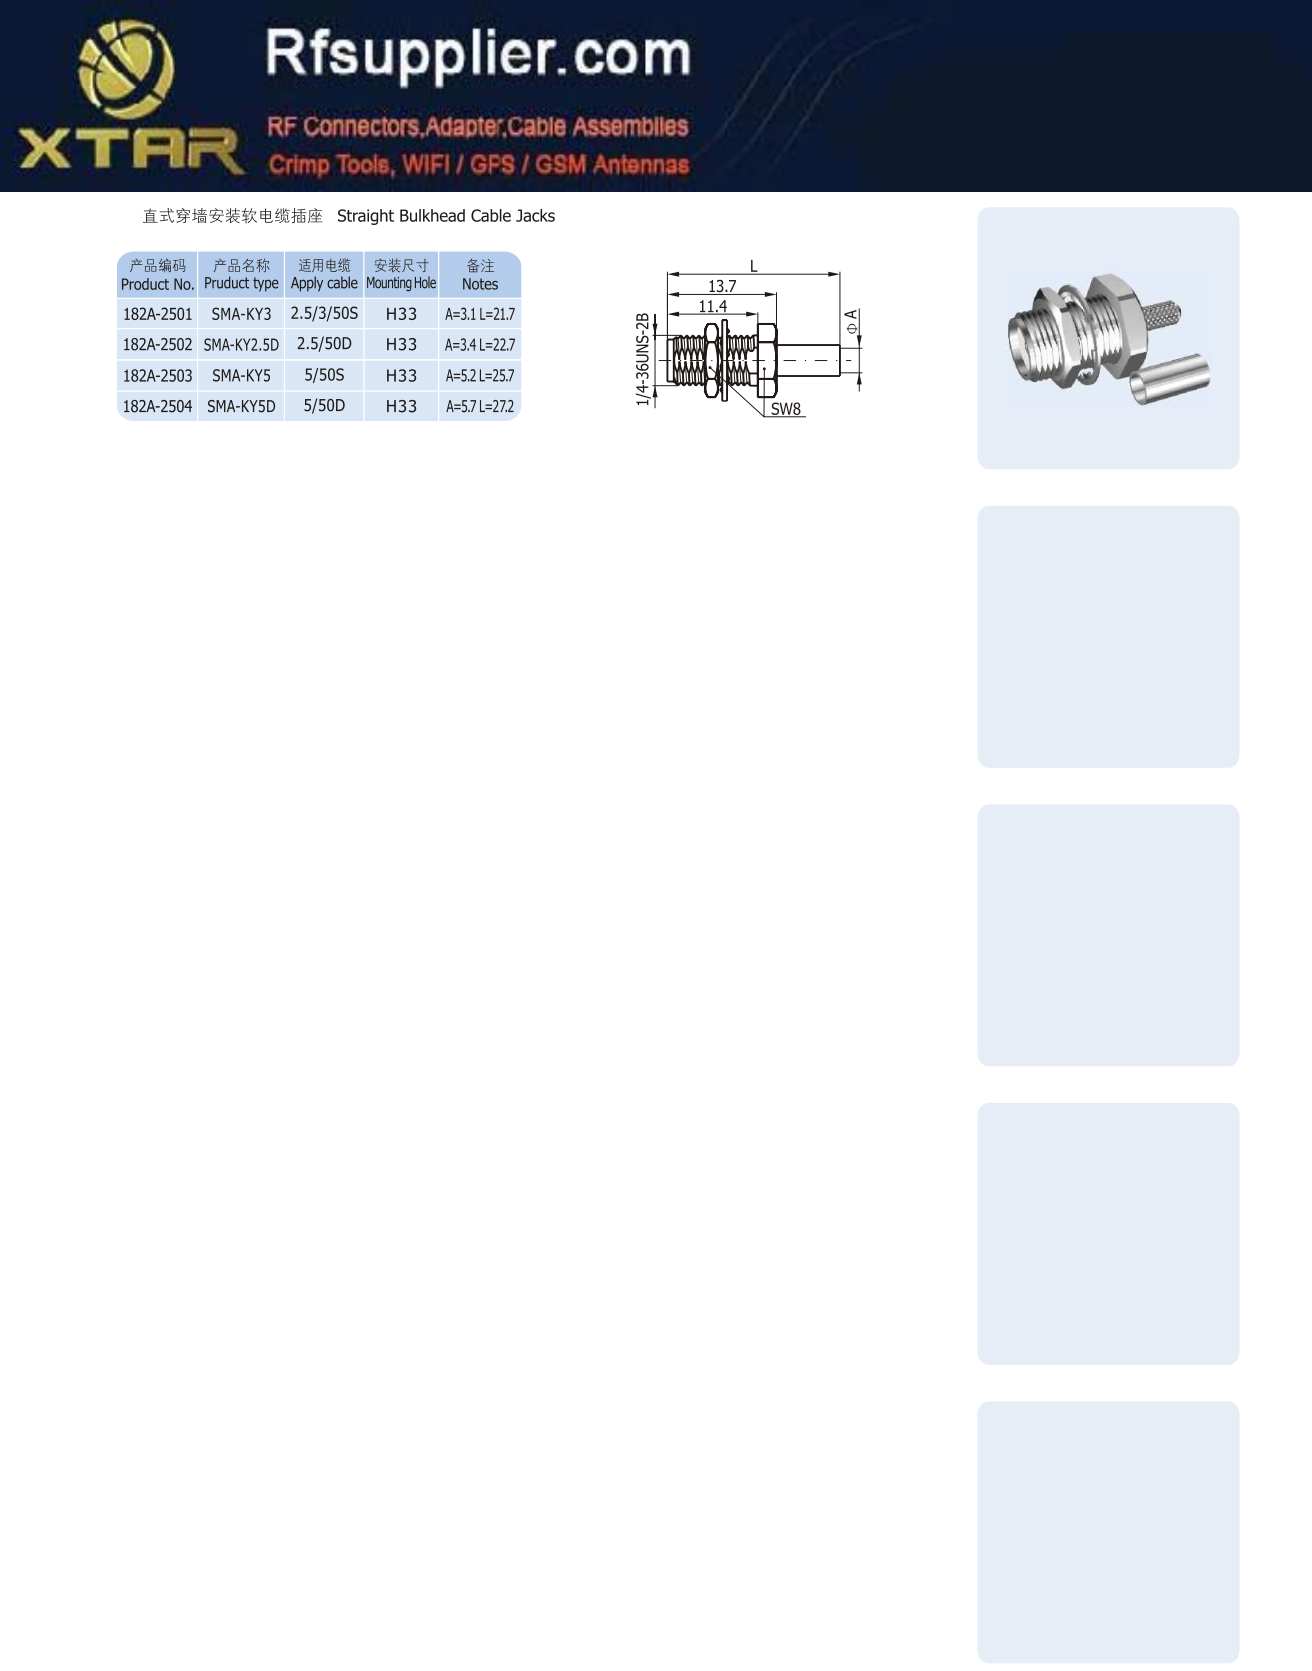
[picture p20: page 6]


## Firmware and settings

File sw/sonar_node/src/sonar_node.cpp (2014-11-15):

#include <ros/ros.h>
#include <stdio.h>
#include <stdlib.h>
#include <math.h>
#include <vector>
#include <fftw3.h>
#include <cstring>
#include <time.h>

#include "sonar/sonar_utils.h"
#include "sonar/sonar_fft.h"
#include "sonar/cheetah.h"

#include "sonar_node/Pinger.h"
#include "sonar_node/PingerArray.h"
#include "sonar_node/FindPingers.h"

// Globals
const double SPEED_SOUND_WATER     = 1482;  // [m/s]
const double SENSOR_SPACING_2_1    = 0.024; // [m]
const double SENSOR_SPACING_3_2    = 0.024; // [m]
const double SENSOR_SPACING_1_3    = 0.024; // [m]
const int    DATA_BLOCK_SIZE       = 512;
const int    DATA_RETENTION_LENGTH = 3 * DATA_BLOCK_SIZE;

// Declare Cheetah Variables
Cheetah    handle;
int        port, bitrate;
uint8_t    mode = 0;
int        ret, input, ready_bit, valid_data_point;

// FFT & Bin Prediction
const int  FP_FFT_LENGTH     = 32;  // First-pass FFT length
double     BIN_PREDICTION_M  = 10.59;
double     BIN_PREDICTION_B  = -1193.82;
int        target_frequency1 = 25000;
int        target_frequency2 = 23000;
double     target_wavelength1, target_wavelength2;
double     angle_estimate1, angle_estimate2;
double     bin_current_mag_sq_1, bin_current_mag_sq_2, bin_current_mag_sq_3;
double     adc1_bin_mean, adc2_bin_mean, adc3_bin_mean;
std::vector<bool> FP_bin_indicator;

// Raw Data
const int  TX_LENGTH = DATA_BLOCK_SIZE * 3 * 2;
uint8_t    data_in[TX_LENGTH];
uint8_t    data_out[2];

// Hysterisis Vars
const int FP_BIN_HISTORY_LENGTH = 10;
const double MEAN_SCALE_FACTOR = 10.0;
const int FP_MIN_SAMPLE_LENGTH = 128;
int FP_bin_mean_idx = 1;
double FP_adc1_bin_history[FP_BIN_HISTORY_LENGTH];
double FP_adc2_bin_history[FP_BIN_HISTORY_LENGTH];
double FP_adc3_bin_history[FP_BIN_HISTORY_LENGTH];
int    FP_bin_history_fill = 0;
std::vector<double> *adc1_data_buffer, *adc2_data_buffer, *adc3_data_buffer, *tmp_data_buffer;

// ROS
ros::ServiceServer * FindPingers_srv;

sonar_node::Pinger pinger0;
sonar_node::Pinger pinger1;
time_t time_pinger0, time_pinger1, now;

void initPingers() {
  pinger0.Id = 0;
  pinger0.Heading = 0;
  pinger0.Magnitude = 0;
  pinger0.TimeSince = -1;
  
  pinger1.Id = 1;
  pinger1.Heading = 0;
  pinger1.Magnitude = 0;
  pinger1.TimeSince = -1;
}


bool FindPingersCallback(sonar_node::FindPingers::Request & req, sonar_node::FindPingers::Response & resp) {
  time(&now);
  switch ((int)req.PingerIDs.size()) {
    case 1:
      ROS_INFO("got a request to announce pinger %d", req.PingerIDs[0]);
      
      if (req.PingerIDs[0] == 0 && pinger0.TimeSince != -1) {
        pinger0.TimeSince = difftime(now,time_pinger0);
        resp.PingerArray.Pingers.push_back(pinger0);
      } else if (req.PingerIDs[0] == 1 && pinger1.TimeSince != -1) {
        pinger1.TimeSince = difftime(now,time_pinger1);
        resp.PingerArray.Pingers.push_back(pinger1);
      } else {
        ROS_INFO("pinger %d has not been heard yet", req.PingerIDs[0]);
        return false;
      }
        
      break;
    case 2:
      ROS_INFO("got a request to announce both pingers");
      
      if (pinger0.TimeSince != -1 && pinger1.TimeSince != -1) {
        ROS_INFO("neither pinger has been heard yet");
        return false;
      }
      
      if (pinger0.TimeSince != -1) {
        pinger0.TimeSince = difftime(now,time_pinger0);
        resp.PingerArray.Pingers.push_back(pinger0);
      } else {
        ROS_INFO("pinger 0 has not been heard yet");
      }
      
      if (pinger1.TimeSince != -1) {
        pinger0.TimeSince = difftime(now,time_pinger0);
        resp.PingerArray.Pingers.push_back(pinger1);
      } else {
        ROS_INFO("pinger 1 has not been heard yet");
      }
      break;
    default:
      ROS_ERROR("%d is an invalid number of pingers", (int)req.PingerIDs.size());
      return false;
      break;
  }
  return true;
}


int main (int argc, char *argv[]) {
  if (argc < 2) {
    ROS_ERROR("sonar_node usage: sudo rosrun sonar_node sonar_node PORT [Freq 1] [Freq 1] [Enable debug]\n");
    return 1;
  }
  
  ros::init(argc, argv, "find_pingers");
  ros::NodeHandle n("~");
  
  initPingers();
  ros::ServiceServer FindPingers_srv = n.advertiseService("FindPingers", FindPingersCallback);

  // Initializes Cheetah connection parameters
  port = atoi(argv[1]);
  bitrate = 10000;

  // Estimates sampling frequency
  double sampling_frequency = SeaBee3_Sonar::getSamplingFrequency(bitrate, BIN_PREDICTION_M, BIN_PREDICTION_B);

  // Assigns Target Frequencies
  if (argc >= 3)
    target_frequency1 = atoi(argv[2]);
  if (argc >= 4)
    target_frequency2 = atoi(argv[3]);

  // Determines wavelength of both sonar signals in "pure" water
  target_wavelength1 = (double)SPEED_SOUND_WATER / (double)target_frequency1;
  target_wavelength2 = (double)SPEED_SOUND_WATER / (double)target_frequency2;

  // Declare Data Vectors
  double FP_adc1_samples[FP_FFT_LENGTH], FP_adc2_samples[FP_FFT_LENGTH], FP_adc3_samples[FP_FFT_LENGTH];
  adc1_data_buffer = new std::vector<double>;
  adc2_data_buffer = new std::vector<double>;
  adc3_data_buffer = new std::vector<double>;
  
  // Define and allocate the Data Vectors
  double *data1, *data2, *data3;
  data1 = (double *) fftw_malloc(sizeof(double) * DATA_BLOCK_SIZE);
  data2 = (double *) fftw_malloc(sizeof(double) * DATA_BLOCK_SIZE);
  data3 = (double *) fftw_malloc(sizeof(double) * DATA_BLOCK_SIZE);
  memset(data1, 0, sizeof(double) * DATA_BLOCK_SIZE);
  memset(data2, 0, sizeof(double) * DATA_BLOCK_SIZE);
  memset(data3, 0, sizeof(double) * DATA_BLOCK_SIZE);
  
  // Open the device
  handle = ch_open(port);

  if (handle <= 0) {
    ROS_ERROR("Unable to open Cheetah device on port %d (Error code = %d: %s)", port, handle, ch_status_string(handle));
    exit(1);
  }
  ROS_INFO("Opened Cheetah device on port %d", port);

  ROS_INFO("Host interface is %s",
      (ch_host_ifce_speed(handle)) ? "high speed" : "full speed");

  // Ensure that the SPI subsystem is configured.
  ch_spi_configure(handle, CheetahSpiPolarity(mode >> 1), CheetahSpiPhase(mode & 1), CH_SPI_BITORDER_MSB, 0x0);
  ROS_INFO("SPI configuration set to mode %d, %s shift, SS[2:0] active low", mode, "MSB");

  // Power the target using the Cheetah adapter's power supply.
  ch_target_power(handle, CH_TARGET_POWER_ON);
  ch_sleep_ms(100);

  // Set the bitrate.
  bitrate = ch_spi_bitrate(handle, bitrate);
  ROS_INFO("Bitrate set to %d kHz", bitrate);

  // Make a simple queue to just assert OE.
  ch_spi_queue_clear(handle);
  ch_spi_queue_oe(handle, 1);
  ch_spi_batch_shift(handle, 0, 0);

  // Queue the batch, which is a sequence of SPI packets (back-to-back) each of length 2.
  ROS_DEBUG("Beginning to queue SPI packets...");
  data_out[0] = 0xff;
  data_out[1] = 0xff;
  ch_spi_queue_clear(handle);
  
  for (int i = 0; i < DATA_BLOCK_SIZE; ++i) {
    // Convert Slave 1
    ch_spi_queue_ss(handle, 0xF);
    ch_spi_queue_array(handle, 2, data_out);
    ch_spi_queue_ss(handle, 0xE);
    
    // Convert Slave 2
    ch_spi_queue_ss(handle, 0xF);
    ch_spi_queue_array(handle, 2, data_out);
    ch_spi_queue_ss(handle, 0xD);
    
    // Convert Slave 3
    ch_spi_queue_ss(handle, 0xF);
    ch_spi_queue_array(handle, 2, data_out);
    ch_spi_queue_ss(handle, 0xB);
  }
  ROS_DEBUG("Done queueing packets");
  
  // Submit the first batch
  ch_spi_async_submit(handle);

  while (ros::ok()) {
    //fprintf(stderr, "Starting Loop!\n");
    // Submit another batch, while the previous one is in
    // progress.  The application may even clear the current
    // batch queue and queue a different set of SPI
    // transactions before submitting this batch
    // asynchronously.
    ch_spi_async_submit(handle);
    
    // The application can now perform some other functions
    // while the Cheetah is both finishing the previous batch
    // and shifting the current batch as well.  In order to
    // keep the Cheetah's pipe full, this entire loop must
    // complete AND another batch must be submitted
    // before the current batch completes.
    //ch_sleep_ms(1);
    
    // Collect the previous batch
    // The length of the batch, FP_FFT_LENGTH * 6, come from the fact that 3 ADCs
    // are batched and the return data requires 2 bytes.  (2 * 3 = 6)
    ret = ch_spi_async_collect(handle, TX_LENGTH, data_in);

    int data_idx = 0;
    for (int j = 0; j < TX_LENGTH; j += 6) {
      // SS3 Data
      input = (data_in[j] << 8) + data_in[j+1];
      ready_bit = input & 0x4000;
      valid_data_point = (input & 0x3ffc) >> 2;
      data3[data_idx] = valid_data_point;

      // SS1 Data
      input = (data_in[j+2] << 8) + data_in[j+3];
      ready_bit = input & 0x4000;
      valid_data_point = (input & 0x3ffc) >> 2;
      data1[data_idx] = valid_data_point;

      // SS2 Data
      input = (data_in[j+4] << 8) + data_in[j+5];
      ready_bit = input & 0x4000;
      valid_data_point = (input & 0x3ffc) >> 2;
      data2[data_idx] = valid_data_point;
      ++data_idx;
    }
    
    // Append current data to history vectors
    adc1_data_buffer->insert(adc1_data_buffer->end(), data1, data1 + DATA_BLOCK_SIZE);
    adc2_data_buffer->insert(adc2_data_buffer->end(), data2, data2 + DATA_BLOCK_SIZE);
    adc3_data_buffer->insert(adc3_data_buffer->end(), data3, data3 + DATA_BLOCK_SIZE);

    
    //ROS_DEBUG("Vector Length: %d\n", adc1_data_buffer->size());
    for (int vector_idx = 0; vector_idx <= (int)adc1_data_buffer->size() - FP_FFT_LENGTH; vector_idx += FP_FFT_LENGTH) {
      //ROS_DEBUG("Copying vector memory\n");
      std::copy(adc1_data_buffer->begin() + vector_idx, adc1_data_buffer->begin() + vector_idx + FP_FFT_LENGTH, FP_adc1_samples);
      std::copy(adc2_data_buffer->begin() + vector_idx, adc2_data_buffer->begin() + vector_idx + FP_FFT_LENGTH, FP_adc2_samples);
      std::copy(adc3_data_buffer->begin() + vector_idx, adc3_data_buffer->begin() + vector_idx + FP_FFT_LENGTH, FP_adc3_samples);
      //ROS_DEBUG("Done copying vector memory\n");
      
/*      for (int i = 0; i < FP_FFT_LENGTH; ++i)
        ROS_DEBUG("%5.0f", FP_adc1_samples[i]);
      ROS_DEBUG("\n");*/
      
      //ROS_DEBUG("Prepping DataToFFT\n");
      SeaBee3_Sonar::DataToFFT fp_fft_f1 = SeaBee3_Sonar::DataToFFT(FP_adc1_samples, FP_adc2_samples, FP_adc3_samples,
                                                                    FP_FFT_LENGTH, sampling_frequency, target_frequency1);
      SeaBee3_Sonar::DataToFFT fp_fft_f2 = SeaBee3_Sonar::DataToFFT(FP_adc1_samples, FP_adc2_samples, FP_adc3_samples,
                                                                    FP_FFT_LENGTH, sampling_frequency, target_frequency2);
      //ROS_DEBUG("Done prepping DataToFFT\n");
      
      bin_current_mag_sq_1 = fp_fft_f1.getMagnitude(1);
      bin_current_mag_sq_2 = fp_fft_f1.getMagnitude(2);
      bin_current_mag_sq_3 = fp_fft_f1.getMagnitude(3);
  
      // Index Check
      if (FP_bin_mean_idx >= FP_BIN_HISTORY_LENGTH)
        FP_bin_mean_idx = 0;
  
      // Initilize Mean Array
      if (FP_bin_history_fill < FP_BIN_HISTORY_LENGTH) {
        FP_adc1_bin_history[FP_bin_mean_idx] = bin_current_mag_sq_1;
        FP_adc2_bin_history[FP_bin_mean_idx] = bin_current_mag_sq_2;
        FP_adc3_bin_history[FP_bin_mean_idx] = bin_current_mag_sq_3;
        ++FP_bin_mean_idx;
        ++FP_bin_history_fill;
        continue;
      }
      
      // Calculates the mean of the bin history
      // This is used to detect the beginning of a ping block packet
      adc1_bin_mean = 0;
      adc2_bin_mean = 0;
      adc3_bin_mean = 0;
      
      for (int i = 0; i < FP_BIN_HISTORY_LENGTH; ++i) {
        adc1_bin_mean += FP_adc1_bin_history[i];
        adc2_bin_mean += FP_adc2_bin_history[i];
        adc3_bin_mean += FP_adc3_bin_history[i];
      }
      adc1_bin_mean /= (double)FP_BIN_HISTORY_LENGTH;
      adc2_bin_mean /= (double)FP_BIN_HISTORY_LENGTH;
      adc3_bin_mean /= (double)FP_BIN_HISTORY_LENGTH;

      // If all bin magnitudes are sufficiently large with respect to the history mean,
      if (bin_current_mag_sq_1 > MEAN_SCALE_FACTOR * adc1_bin_mean &&
          bin_current_mag_sq_2 > MEAN_SCALE_FACTOR * adc2_bin_mean &&
          bin_current_mag_sq_3 > MEAN_SCALE_FACTOR * adc3_bin_mean) {
        // note a positive block (don't modify the means)
        FP_bin_indicator.push_back(true);
        ROS_DEBUG("1 ");
        ROS_DEBUG("%15.0f\n", bin_current_mag_sq_3);
      } else {
        // note a negative block.
        FP_bin_indicator.push_back(false);
        //ROS_DEBUG("0 ");
        //ROS_DEBUG("%15.0f\n", bin_current_mag_sq_3);

        // adjust the bin history values
        FP_adc1_bin_history[FP_bin_mean_idx] = bin_current_mag_sq_1;
        FP_adc2_bin_history[FP_bin_mean_idx] = bin_current_mag_sq_2;
        FP_adc3_bin_history[FP_bin_mean_idx] = bin_current_mag_sq_3;
        //ROS_DEBUG("%10.0f, %10.0f, %10.0f\n", adc1_bin_mean, adc2_bin_mean, adc3_bin_mean);
        ++FP_bin_mean_idx;
      }
      
      // Checks state transition from positive to negative ping detection
      // If the end of a ping is detected, consider it for phase analysis
      if (FP_bin_indicator[0] == 0 && FP_bin_indicator[1] == 1) {
        ROS_DEBUG("Just had a pulse!\n");
        
        // Counts the number of blocks with detected pings
        int SP_bin_count = 0;
        while (FP_bin_indicator[SP_bin_count + 1] != 0)
          ++SP_bin_count;
        ROS_DEBUG("Signal Bin Count of %d\n", SP_bin_count);
        
        // If the duration of the ping is sufficiently long, continue analysis
        if (SP_bin_count * FP_FFT_LENGTH >= FP_MIN_SAMPLE_LENGTH) {
          int SP_fft_length = SP_bin_count * FP_FFT_LENGTH;
          
          // Copies the sample data into new double array
          double *SP_adc1_samples = new double[SP_fft_length];
          double *SP_adc2_samples = new double[SP_fft_length];
          double *SP_adc3_samples = new double[SP_fft_length];
          
          // Copies signal segment containing ping
          std::copy(adc1_data_buffer->begin() + vector_idx - (SP_bin_count) * FP_FFT_LENGTH, adc1_data_buffer->begin() + vector_idx, SP_adc1_samples);
          std::copy(adc2_data_buffer->begin() + vector_idx - (SP_bin_count) * FP_FFT_LENGTH, adc2_data_buffer->begin() + vector_idx, SP_adc2_samples);
          std::copy(adc3_data_buffer->begin() + vector_idx - (SP_bin_count) * FP_FFT_LENGTH, adc3_data_buffer->begin() + vector_idx, SP_adc3_samples);
          
          // Deletes all data history up to and including the detected ping to prevent duplication
          adc1_data_buffer->erase(adc1_data_buffer->begin(), adc1_data_buffer->begin() + vector_idx);
          adc2_data_buffer->erase(adc2_data_buffer->begin(), adc2_data_buffer->begin() + vector_idx);
          adc3_data_buffer->erase(adc3_data_buffer->begin(), adc3_data_buffer->begin() + vector_idx);
/*          for (int blah = 0; blah < FP_FFT_LENGTH; ++blah)
            ROS_DEBUG("%5.0f", FP_adc1_samples[blah]);
          ROS_DEBUG("\n\n\n\n");*/
          
          SeaBee3_Sonar::DataToFFT sp_fft_f1 = SeaBee3_Sonar::DataToFFT(FP_adc1_samples, FP_adc2_samples, FP_adc3_samples,
                                          FP_FFT_LENGTH, sampling_frequency, target_frequency1);
          SeaBee3_Sonar::DataToFFT sp_fft_f2 = SeaBee3_Sonar::DataToFFT(FP_adc1_samples, FP_adc2_samples, FP_adc3_samples,
                                          FP_FFT_LENGTH, sampling_frequency, target_frequency2);
          
          ROS_DEBUG("SP Target Bin: %d\n", sp_fft_f1.getTargetBin());
          
          // Extracts signal phase
          double phase1 = sp_fft_f1.getPhase(1);
          double phase2 = sp_fft_f1.getPhase(2);
          double phase3 = sp_fft_f1.getPhase(3);
          
          // Calculates usable phase differences
          double delta1 = phase2 - phase1;
          double delta2 = phase3 - phase2;
          double delta3 = phase1 - phase3;
          
          ROS_DEBUG("Phase: %5.5f  %5.5f  %5.5f\n", phase1, phase2, phase3);
          ROS_DEBUG("Deltas: %5.5f  %5.5f  %5.5f\n", delta1, delta2, delta3);
          
          // Determines minimum phase difference for hydrophone pair selection
          int min_index = 3;
          if (fabs(delta2) < fabs(delta1) && fabs(delta2) < fabs(delta3))
            min_index = 2;
          if (fabs(delta1) < fabs(delta2) && fabs(delta1) < fabs(delta3))
            min_index = 1;

          // Calculates angle estimate based on best input pair
          double delta_tmp;
          switch (min_index) {
            case 1:
              delta_tmp = delta1;
              if (delta3 > delta2)
                delta_tmp = -1.0 * delta1 + SeaBee3_Sonar::sign(delta_tmp) * 2.0 * M_PI;
              angle_estimate1 = delta_tmp * (double)(((double)target_wavelength1 / 2.0) / SENSOR_SPACING_2_1) * 180.0 / M_PI / 2.0;
              break;
            case 2:
              delta_tmp = delta2;
              if (delta1 > delta3)
                delta_tmp = -1.0 * delta2 + 2.0 * M_PI;
              angle_estimate1 = (delta_tmp - 4.0 / 3.0 * M_PI) * ((target_wavelength1 / 2.0) / SENSOR_SPACING_3_2) * 180.0 / M_PI / 2.0;
              break;
            case 3:
              delta_tmp = delta3;
              if (delta2 > delta1)
                delta_tmp = -1.0 * delta3 - 2.0 * M_PI;
              angle_estimate1 = (delta_tmp + 4.0 / 3.0 * M_PI ) * (((double)target_wavelength1 / 2.0) / SENSOR_SPACING_1_3) * 180.0 / M_PI / 2.0;
              break;
            default:
              ROS_ERROR("Sonar: Invalid min_index for phase difference.");
          }
          ROS_DEBUG("Min Index: %d\n", min_index);
          ROS_DEBUG("Angle Estimate (1): %3.2f\n", angle_estimate1);
          
          pinger0.Heading   = angle_estimate1;
          pinger0.Magnitude = (sp_fft_f1.getMagnitude(1) +
                               sp_fft_f1.getMagnitude(2) +
                               sp_fft_f1.getMagnitude(3)) / 3.0;
          pinger0.TimeSince = 0;
          time (&time_pinger0);
          
/*          // DEBUG
          for (int blah = 0; blah < SP_bin_count * FP_FFT_LENGTH; ++blah)
            ROS_DEBUG("%5.0f", SP_adc1_samples[blah]);
          ROS_DEBUG("\n");*/
          
        }
      }
  
    // Check that data history length constraints are satisfied
    // This prevents too much data building up in the buffers in order to reduce computation time.
    if ((int)adc1_data_buffer->size() > DATA_RETENTION_LENGTH) {
      //ROS_DEBUG("Data history is too long, reducing vector sizes\n");
      tmp_data_buffer = new std::vector<double> (adc1_data_buffer->begin() + adc1_data_buffer->size() - DATA_RETENTION_LENGTH, adc1_data_buffer->end());
      delete adc1_data_buffer;
      adc1_data_buffer = tmp_data_buffer;
      tmp_data_buffer = NULL;
    }
    if ((int)adc2_data_buffer->size() > DATA_RETENTION_LENGTH) {
      tmp_data_buffer = new std::vector<double> (adc2_data_buffer->begin() + adc2_data_buffer->size() - DATA_RETENTION_LENGTH, adc2_data_buffer->end());
      delete adc2_data_buffer;
      adc2_data_buffer = tmp_data_buffer;
      tmp_data_buffer = NULL;
    }
    if ((int)adc3_data_buffer->size() > DATA_RETENTION_LENGTH) {
      tmp_data_buffer = new std::vector<double> (adc3_data_buffer->begin() + adc3_data_buffer->size() - DATA_RETENTION_LENGTH, adc3_data_buffer->end());
      delete adc3_data_buffer;
      adc3_data_buffer = tmp_data_buffer;
      tmp_data_buffer = NULL;
    }
    
    if ((int)FP_bin_indicator.size() > FP_BIN_HISTORY_LENGTH)
      FP_bin_indicator.erase(FP_bin_indicator.begin());
    }
    ros::spinOnce();
  }

  return 0;
}

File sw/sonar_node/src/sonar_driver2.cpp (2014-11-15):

/*=========================================================================
| (c) 2005-2007  Total Phase, Inc.
|--------------------------------------------------------------------------
| Project : Cheetah Sample Code
| File    : async.c
|--------------------------------------------------------------------------
| Use the asynchronous interface of the Cheetah host adapter
|--------------------------------------------------------------------------
| Redistribution and use of this file in source and binary forms, with
| or without modification, are permitted.
|
| THIS SOFTWARE IS PROVIDED BY THE COPYRIGHT HOLDERS AND CONTRIBUTORS
| "AS IS" AND ANY EXPRESS OR IMPLIED WARRANTIES, INCLUDING, BUT NOT
| LIMITED TO, THE IMPLIED WARRANTIES OF MERCHANTABILITY AND FITNESS
| FOR A PARTICULAR PURPOSE ARE DISCLAIMED.  IN NO EVENT SHALL THE
| COPYRIGHT OWNER OR CONTRIBUTORS BE LIABLE FOR ANY DIRECT, INDIRECT,
| INCIDENTAL, SPECIAL, EXEMPLARY, OR CONSEQUENTIAL DAMAGES (INCLUDING,
| BUT NOT LIMITED TO, PROCUREMENT OF SUBSTITUTE GOODS OR SERVICES;
| LOSS OF USE, DATA, OR PROFITS; OR BUSINESS INTERRUPTION) HOWEVER
| CAUSED AND ON ANY THEORY OF LIABILITY, WHETHER IN CONTRACT, STRICT
| LIABILITY, OR TORT (INCLUDING NEGLIGENCE OR OTHERWISE) ARISING IN
| ANY WAY OUT OF THE USE OF THIS SOFTWARE, EVEN IF ADVISED OF THE
| POSSIBILITY OF SUCH DAMAGE.
 ========================================================================*/

//=========================================================================
// INCLUDES
//=========================================================================
#include <stdio.h>
#include <stdlib.h>
#include <string.h>
#include "cheetah.h"
#include <ros/ros.h>
#include <iostream>
#include <fstream>


// Globals
const int       NUM_SAMPLES             = 1000000;
const int       DATA_BLOCK_SIZE         = NUM_SAMPLES * 3; //#of ADCs
const int       TX_LENGTH = DATA_BLOCK_SIZE * 2;
uint8_t         data_in[TX_LENGTH]; //raw data
uint8_t         data_out[2];
long int        data1[TX_LENGTH/3];
long int        data2[TX_LENGTH/3];
long int        data3[TX_LENGTH/3];

// Declare Cheetah Variables
Cheetah         handle;
int             port, bitrate;
uint8_t         mode = 0;
int             ret, input, ready_bit, valid_data_point;
	// Open output filestreams
	std::ofstream file1 ("1_adc_samples.txt");
	std::ofstream file2 ("2_adc_samples.txt");
	std::ofstream file3 ("3_adc_samples.txt");

#ifdef _WIN32
#include <time.h>
#else
#include <sys/time.h>
#endif


//=========================================================================
// CONSTANTS
//=========================================================================
// Uncomment to show the data returned by the shifting device
#define SHOW_DATA

// Add a delay between bytes by changing this constant (in nanoseconds)
#define BYTE_DELAY 0


//=========================================================================
// UTILITY FUNCTIONS
//=========================================================================
static s64 _timeMillis () {
#ifdef _WIN32
    return ((s64)clock()) * 1000 / CLOCKS_PER_SEC;
#else
    struct timeval tv;
    gettimeofday(&tv, 0);
    return ((s64)tv.tv_sec * 1000L) + (s64)(tv.tv_usec / 1000L);
#endif
}


//=========================================================================
// FUNCTIONS
//=========================================================================
static void _blast_async (Cheetah handle, u32 txnlen, u32 iter) {
    double elapsed;
    u32    i;
    int    count = 0;
    u08    data_out[4];
    s64    start;
    int    ret;

    // Make a simple queue to just assert OE.
    ch_spi_queue_clear(handle);
    ch_spi_queue_oe(handle, 1);
    ch_spi_batch_shift(handle, 0, 0);

    
    // Queue the batch which is a sequence of SPI packets
    // (back-to-back) each of length 4.
    ch_spi_queue_clear(handle);
    for (i = 0; i < txnlen; ++i) {
       		// Convert Slave 1
	 	ch_spi_queue_ss(handle, 0xF);
	 	ch_spi_queue_array(handle, 2, data_out);
	 	ch_spi_queue_ss(handle, 0xE);

	 	// Convert Slave 2
	 	ch_spi_queue_ss(handle, 0xF);
	 	ch_spi_queue_array(handle, 2, data_out);
	 	ch_spi_queue_ss(handle, 0xD);

	 	// Convert Slave 3
	 	ch_spi_queue_ss(handle, 0xF);
	 	ch_spi_queue_array(handle, 2, data_out);
	 	ch_spi_queue_ss(handle, 0xB);
    }


    start = _timeMillis();

    // First, submit first batch 
    ch_spi_async_submit(handle);

    for (i = 0; i < iter-1; ++i) {
        // Submit another batch, while the previous one is in
        // progress.  The application may even clear the current
        // batch queue and queue a different set of SPI
        // transactions before submitting this batch
        // asynchronously.
        ch_spi_async_submit(handle);
        
        // The application can now perform some other functions
        // while the Cheetah is both finishing the previous batch
        // and shifting the current batch as well.  In order to
        // keep the Cheetah's pipe full, this entire loop must
        // complete AND another batch must be submitted
        // before the current batch completes.
        ch_sleep_ms(25);
        
        // Collect the previous batch
        ret = ch_spi_async_collect(handle, 0, 0);
        elapsed = ((double)(_timeMillis() - start)) / 1000;
        printf("collected batch #%03d in %.2lf seconds\n", i+1, elapsed);
        if (ret < 0)  printf("status error: %s\n", ch_status_string(ret));
        fflush(stdout);

        start = _timeMillis();
        
        // The current batch is now shifting out on the SPI
        // interface. The application can again do some more tasks
        // here but this entire loop must finish so that a new
        // batch is armed before the current batch completes.
        ch_sleep_ms(25);
    }

    // Collect batch the last batch
    ret = ch_spi_async_collect(handle, 0, 0);
    elapsed = ((double)(_timeMillis() - start)) / 1000;
    printf("collected batch #%03d in %.2lf seconds\n", i+1, elapsed);
    if (ret < 0)  printf("status error: %s\n", ch_status_string(ret));
    fflush(stdout);
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

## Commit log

2014-11-15 Added ROS sonar_node software.
2014-11-16 Added more camera images.
2014-12-13 Added docs, hw.
    [Arduino.SchDoc, Data Acquisition Schematic.SchDoc, Sonar_Rev2.PrjPCB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]
2015-02-27 Pulled new files from old HD.
    [lookup_tbl.xlsx]
2015-04-17 Added sonar 3d files
    [sonar.step, sonar_DAQ.stp, sonar_DAQ_single.stp]
